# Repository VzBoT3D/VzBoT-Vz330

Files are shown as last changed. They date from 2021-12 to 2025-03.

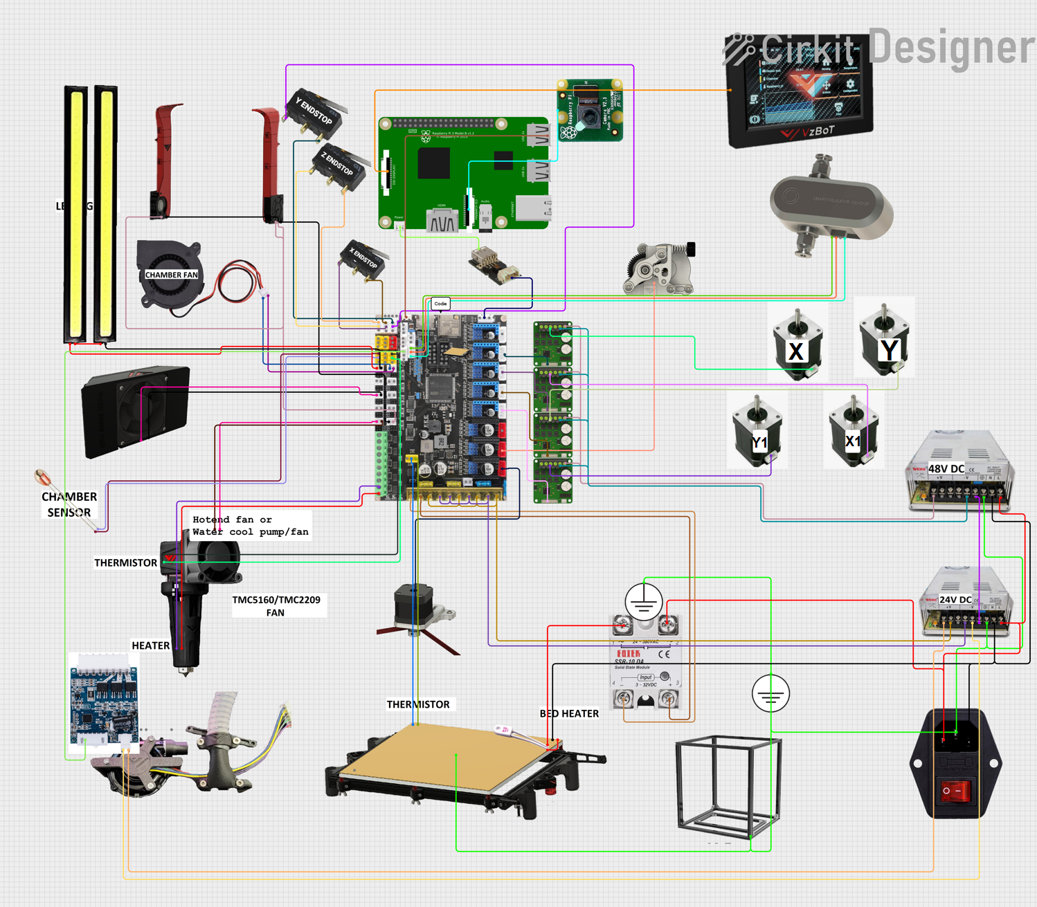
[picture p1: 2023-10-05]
Wiring Diagram/VZBOT 330 WIRING DIAGRAM AWD WITH CPAP.png

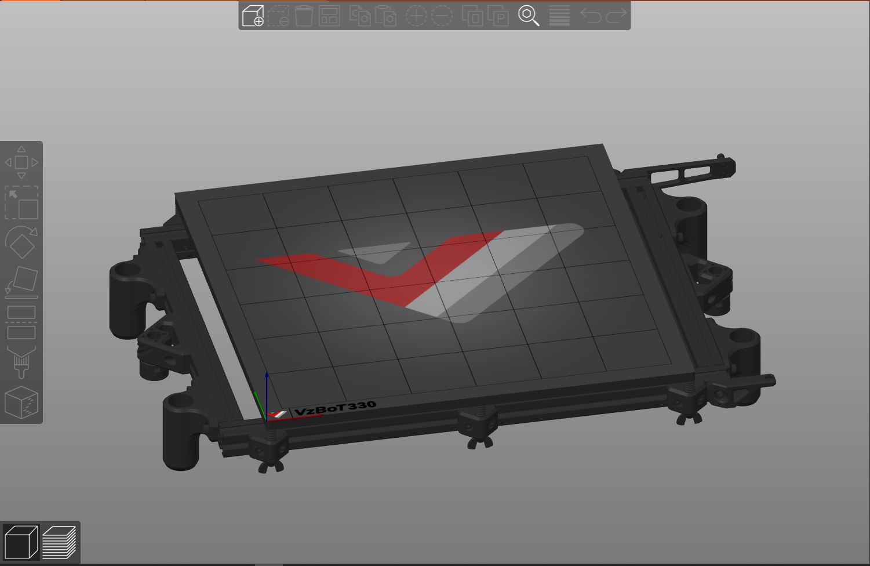
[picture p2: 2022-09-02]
Slicer/Theme/PrusaSlicer-SuperSlicer/Gallery/Vz330_bed_showcase.JPG

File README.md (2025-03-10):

# VzBoT <a href='https://ko-fi.com/vez3d' target='_blank'>Buy Me a Coffee at ko-fi.com</a> 

Discord Invite (https://discord.gg/KWZWvCMxCq)

High speed, moderately sized 3D-printer, based on the TronXY XS5(A) CoreXY frame,
but can be easily adapted for other 2020 aluminium extrusion frames.

You can find the complete web model without CAD-Software here: 
- [Printed Vz-330](https://a360.co/3FtdnGd)  
- [Full CNC AWD Vz-330](https://a360.co/4iu8HhW)

Vz-330-printed

Buy the full printer kit here: <https://s.click.aliexpress.com/e/_DkFwymp>

# Looking For Guides?

The VzBoT team has been working on our own docs for helping with your assembly of the machine. For the most upto date guides they can be found on the [VzBoT Docs][].

[VzBoT Docs]: https://docs.vzbot.org/

# What is the VzBoT?
The VzBoT is a high speed, moderately sized 3d Printer. Originally based on the TronXY X5S / X5SA Frame, this printer was aimed at those who wanted more performance out of their 330x330mm sized CoreXY 3D-printer.

Since this era, the VzBoT project has come very far. With CNC aluminum parts and a full kit with custom high performance hotend, the project has evolved at a lightning pace to be one of the fastest printers out there.

The printers
Originally, the VZ project started with a Vz-330 by Simon Vez. Recently, Guillaume has developed his iteration of the VzBoT. This printer aims to address a few compromises with the larger sized printer, by using a 235x235 bed size (ender 3 sized). This makes sourcing the parts for this printer relatively easy. Combined with the AWD functionality (all wheel drive, 2 motors on X and 2 on Y) and shorter belt loops, this printer is for those who thrive to be the fastest.

# What will a VzBoT set me back in terms of money?
Originally, as of start of 2022, a Vz-330 would set you back as follows:

800$ if you source really well and efficiently (budget)
1000$ for the average VzBoT
1500$ for the whole shablam with alu parts, 48v, all extras etc.

Add 100-150$ for panels, and you've got yourself a very nice 3d printer.

Unfortunately, due to inflation, and other costs, this price may be a higher (think 100-200$).

Additionally, a Vz-235 will be less expensive, due to the smaller size and easily source able parts.

# Where can you buy and find parts?
 We have 2 official manufacturers for parts. Mellow 3D and F3D racing in Germany. There are resellers and we will try to keep this list up to date. Please visit the reseller section

 - F3D Racing: https://f3d-racing-fdm.myshopify.com/
 - Aliexpress and Taobao:  [Mellow Store](https://www.aliexpress.com/store/1531088)

# What is AWD (All wheel drive)?
In conventional CoreXY machines, a 2WD setup is used. This setup utilizes 2 stepper motors at the back or front of the machine. Recently, the VzBoT project has adapted the AWD setup! This setup utilizes 2 motors on X, and 2 on Y, doubling the amount of motors for the XY plane. What are the advantages of this setup? Let's go over them:

- Having two motors on one belt allows for a shorter effective belt length. This leads to less belt stretch, which usually gives better input shaper results.
- The maximum useable acceleration is about 1.5x higher compared to 2WD due to the added torque.

We recommend using the LDO-42STH48-2504AC or 2504AH 1.8deg motors, as they give the best performance for the VzBoT's usecase.

This project is licensed as


https://creativecommons.org/licenses/by-nc/4.0/

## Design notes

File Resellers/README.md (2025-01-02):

List of resellers (this will be updated as we will deploy elwhere)

## Europe:

- Danemark: [3DO.dk](https://3do.dk/) 
- Germany: [CR-3D.de](https://www.cr3d.de/)
- Germany: [Meltbro](https://meltbro.de/mellow-vzbot-awd-330-3d-drucker-bausatz-metall-komponenten-golitath-hotend-hextrudort.html)
- Poland: [X3Dshop](https://x3dshop.com/products/drukarka-3d-mellow-vzbot-330-kit-1)

## Australia:
- [raven3dtech.com.au](https://raven3dtech.com.au/product/mellow-goliath-air-water/)

## Canada 
- [Northprint3d.ca](https://northprint3d.ca/product/vzbot-mellow-goliath-lsd-hotend/) |Only For Goliath|

## USA:
- [Provok3D](https://provok3d.com/vzbot-2/?v=0a10a0b3e53b)
- [3Dprintedprinter](https://3Dprintedprinters.com) 
- [Genericprinter](https://www.genericprinter.com/product/goliath-air-water-v2-hotend/)
- [Print3Dshop.org](https://print3dshop.org/)
- [Fabreeko](https://www.fabreeko.com/collections/hot-ends/products/vz-bot-goliath-hot-end-by-mellow)

## More to come..

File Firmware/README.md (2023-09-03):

- It is meant to work with Mellow Fly Super8 board with TMC5160 HV on XY and TMC2209 on E and Z

# Note for Super 8 Pro with STM32h723 Chip:
## If you are having random MCU disconnection/shutdown, please switch to software SPI, by commenting out the "spi_bus: spi1a" line on each 5160s section and uncomment those 3 lines:

- spi_software_mosi_pin: PB5 
- spi_software_miso_pin: PB4 
- spi_software_sclk_pin: PB3 

# Useful links:
- Super8 and Super8 Pro Documation: https://teamgloomy.github.io/fly_super8_general.html
- Super8 Std Klipper info: https://mellow.klipper.cn/#/board/fly_super8/
- Super8 Pro Klipper info: https://mellow.klipper.cn/#/board/fly_super8_pro/

# DISCLAIMER
- The macro files are REQUIRED for our printer.cfg to work with klipper.
- Its also REQUIRED to add a "Linux Process" to klipper, See the "Install the rc script" and "Building the micro-controller code" section [https://www.klipper3d.org/RPi_microcontroller.html]

# Macros information: DO NOT USE THE SPEED MACROS WITHOUT READING THIS.
## Speed Macros Explanation
Explanation: 
- 1st line: Steps << number of times it will do the stop and go, 100 times in the below case>>
- 2nd line: Velocity/Speed << The speed/velocity at which you want to test. 1000mms here>>
- 3rd line: safety distance << the safety distance in mm that the print head will not go from X max and Y max defined on your printer config>>	
- 4th line: Starting Accel << the starting acceleration value for the test. 10K here>>	

### Credits to DoubleT on Discord for his help on these macros

 [gcode_macro ACCELL_TEST_X]
 
gcode:

    {% set steps = params.STEPS|default(100)|int %}
    {% set speed = params.VELOCITY|default(1000)|float * 60 %}
    
    {% set inset = 10.0|float %} 
    {% set accel = 10000|int %} 
    {% set maxX = printer.configfile.settings.stepper_x.position_max|float - inset %}
    {% set maxY = printer.configfile.settings.stepper_y.position_max|float - inset %}
    {% set minX = printer.configfile.settings.stepper_x.position_min|float + inset %}
    {% set minY = printer.configfile.settings.stepper_y.position_min|float + inset %}

    SAVE_GCODE_STATE NAME=accelltest_state

    SET_VELOCITY_LIMIT ACCEL={accel} 
    SET_VELOCITY_LIMIT ACCEL_TO_DECEL={accel}
    G28
	G1 Z5
    G1 X{minX} Y{minY} F{speed} 

    {% for INTERVAL in range(steps) %}
        {% set eff = accel + (INTERVAL * 1000) %} 
        SET_VELOCITY_LIMIT ACCEL={eff} 
        SET_VELOCITY_LIMIT ACCEL_TO_DECEL={eff}
        G1 X{minX} Y{minY} F{speed}  
        G1 X{maxX} Y{maxY} F{speed}  

    {% endfor %}    

    RESTORE_GCODE_STATE NAME=accelltest_state 

[gcode_macro ACCELL_TEST_Y]

gcode:

    {% set steps = params.STEPS|default(100)|int %}
    {% set speed = params.VELOCITY|default(1000)|float * 60 %}

    {% set inset = 10.0|float %}
    {% set accel = 10000|int %}
    {% set maxX = printer.configfile.settings.stepper_x.position_max|float - inset %}
    {% set maxY = printer.configfile.settings.stepper_y.position_max|float - inset %}
    {% set minX = printer.configfile.settings.stepper_x.position_min|float + inset %}
    {% set minY = printer.configfile.settings.stepper_y.position_min|float + inset %}

    SAVE_GCODE_STATE NAME=accelltest_state

    SET_VELOCITY_LIMIT ACCEL={accel} 
    SET_VELOCITY_LIMIT ACCEL_TO_DECEL={accel}
    G28
	G1 Z5
    G1 X{minX} Y{minY} F{speed} 

    {% for INTERVAL in range(steps) %}
        {% set eff = accel + (INTERVAL * 1000) %} 
        SET_VELOCITY_LIMIT ACCEL={eff} 
        SET_VELOCITY_LIMIT ACCEL_TO_DECEL={eff}
        G1 X{maxX} Y{minY} F{speed}  
        G1 X{minX} Y{maxY} F{speed}  

    {% endfor %}    

    RESTORE_GCODE_STATE NAME=accelltest_state

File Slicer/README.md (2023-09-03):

The Vzbot team has moved Slicers, currently with OrcaSlicer you can download printer ready Profiles!
https://github.com/SoftFever/OrcaSlicer/releases

Thanks to SoftFever for the wondeful Slicer!

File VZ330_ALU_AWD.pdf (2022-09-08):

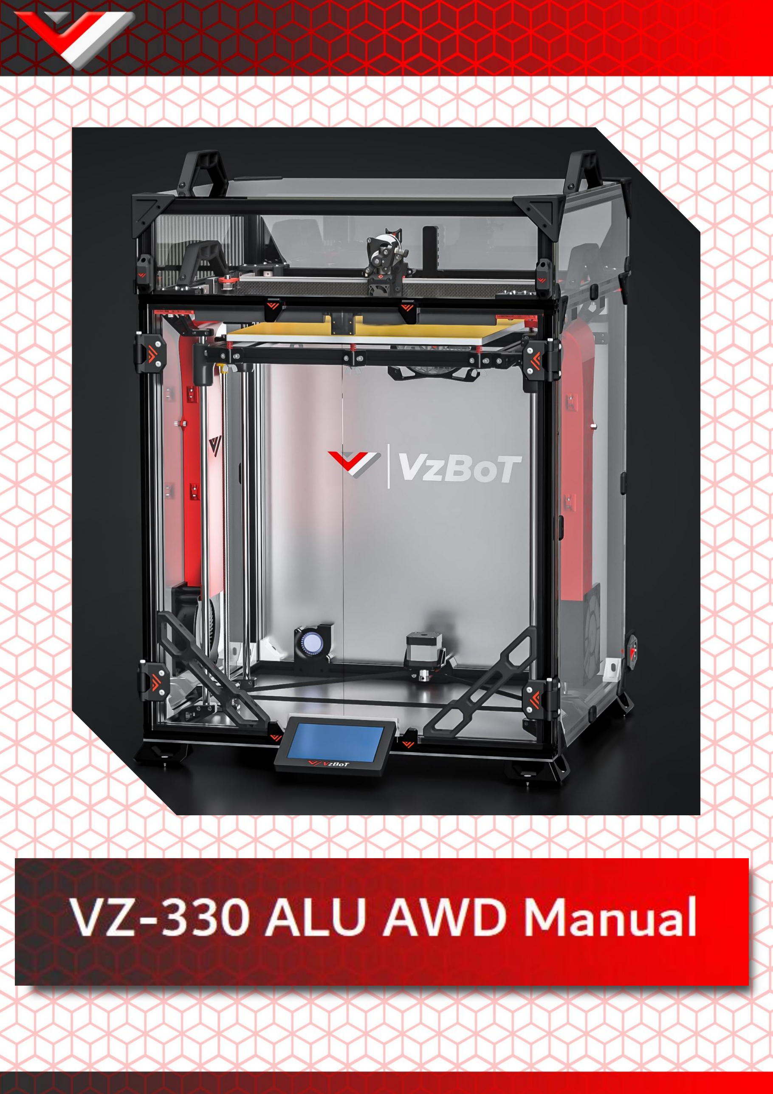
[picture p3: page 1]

## About

This manual is intended for the aluminum parts for VZ330 as sold by F3D-Racing and Mellow. The aluminum parts are interchangeable with the printed parts, some additional hardware is required when purchasing the motor mounts and idler mounts. Furthermore some printed parts are required in order to mount your new sexy parts!

Beware, VZ330 was never designed around AWD like VZ235. Because of this the design team was left with the frame as constraint. Due to which it was not possible to have a design that did not limit y travel for the VZ330 printhead. There is a 10mm loss in Y travel coming from 330mm.

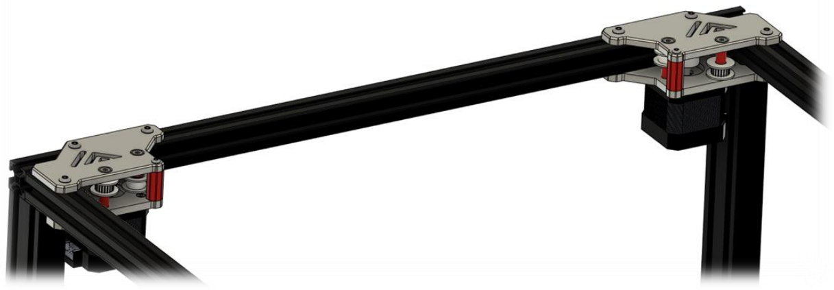
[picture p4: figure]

https://f3d-racing-fdm.myshopify.com/collections/vzbot-vz330

https://mellow.nl.aliexpress.com/store/1531088?spm=a2g0o.detail.1000007.1.67f7726dJR pvIK\ (https://mellow.nl.aliexpress.com/store/1531088?spm=a2g0o.detail.1000007.1.67f7726dJRpvIK/)

*Disclaimer: VzBoT is an opensource passion project, this manual is not definitive, and we try to make it as polished as possible. Fortunately, we all make errors so use common sense when following this guide.

## Print settings:

We recommend printing all parts in ABS, ASA or similar material to be able to withstand the high heat environment in the printer enclosure.

Print settings should always be tuned for your own material and tested for decent strength and layer adhesion.

We recommend the following settings:

For non-moving parts:

Layer height: 0.2mm

Layer with: 0.4 to 0.6 mm

Number of walls: 4

Infill percentage: 40 to 50 %

Top/bottom layers: 5

For moving parts:

Layer height: 0.2mm

Layer with: 0.4 to 0.6 mm

Number of walls: 4

Infill percentage: 30 to 40 % depending on your material

Top/bottom layers: 5

## AWD Motormounts/Idlers

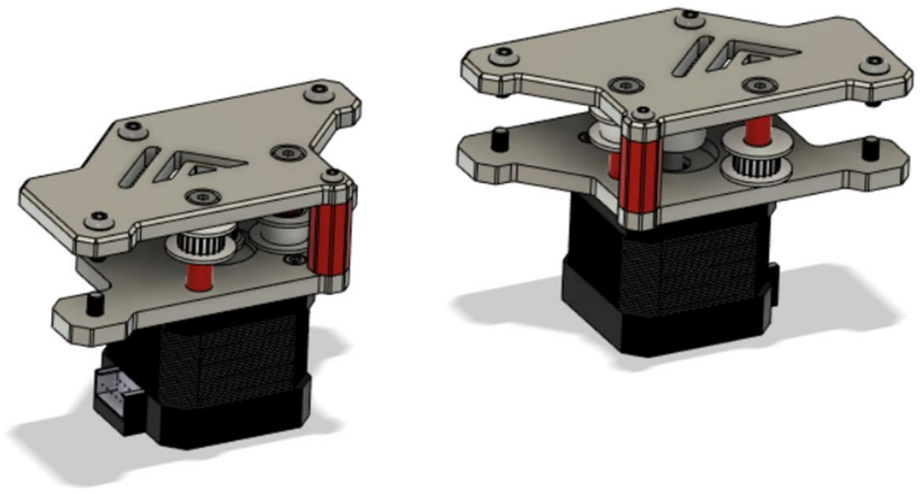
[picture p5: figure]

Bom:

Material | Quantity | Notes
M3 30mm | 2
M3 6mm | 6
M4 10mm | 10 | +2 for mellow version
M4 T-nut | 10
Shoulder bolt 5mmx20mm [M3] | 4 | M3 threading with 6mm of threaded length, if longer grind down the ends. Correct shoulder bolts available at mellow & F3D
GT2 Toothed idler | 2
Gt2 Smooth idler | 2
GT2 motor pulley | 2

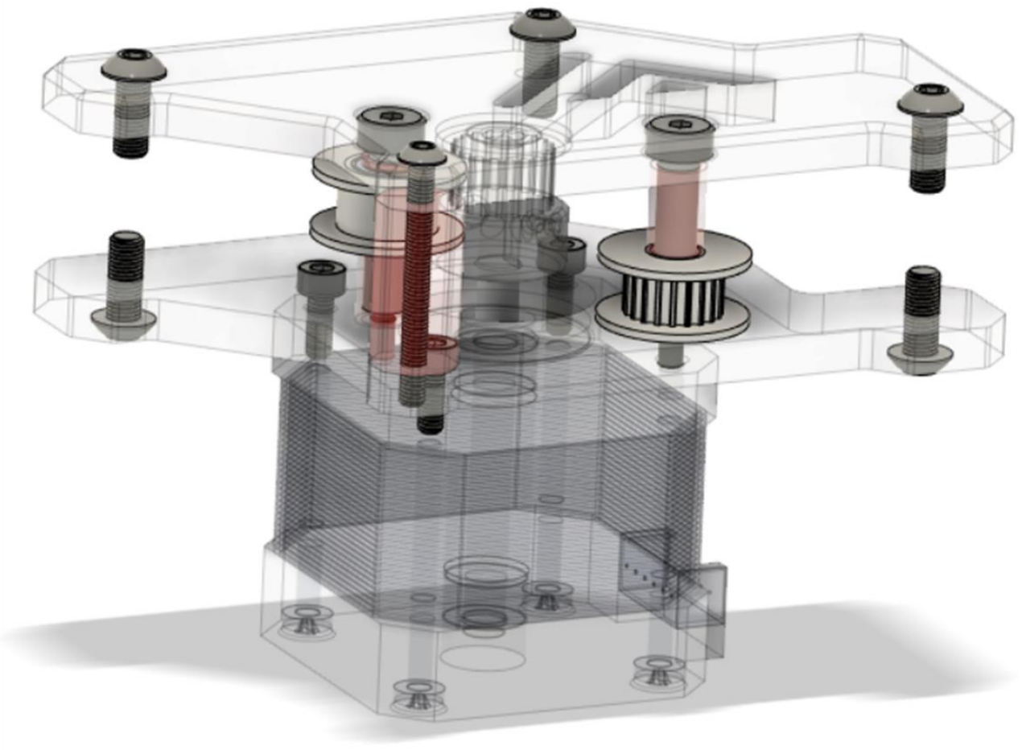
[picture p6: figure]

STL files:

File name | Amount to print
Spacer long | 4
Spacer short bottom | 2
Spacer short top | 2
Spacer M3 corner | 2

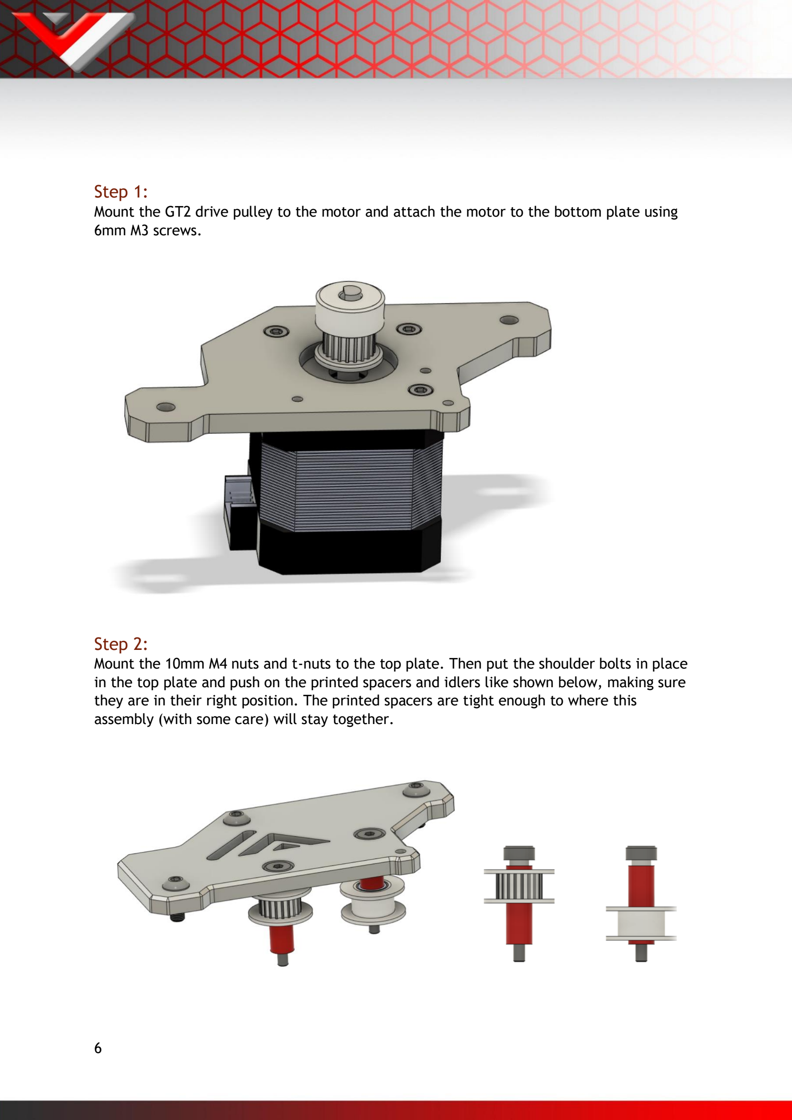
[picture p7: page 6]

Step 1:
Mount the GT2 drive pulley to the motor and attach the motor to the bottom plate using 6mm M3 screws.
Step 2:
Mount the 10mm M4 nuts and t-nuts to the top plate. Then put the shoulder bolts in place in the top plate and push on the printed spacers and idlers like shown below, making sure they are in their right position. The printed spacers are tight enough to where this assembly (with some care) will stay together.

Step 3:
Attach the bottom assembly to the printer frame using 10mm M4 screws and t-nuts. After this attach the top assembly from the previous step loosely. Make sure the shoulder bolts thread before tightening all screws.

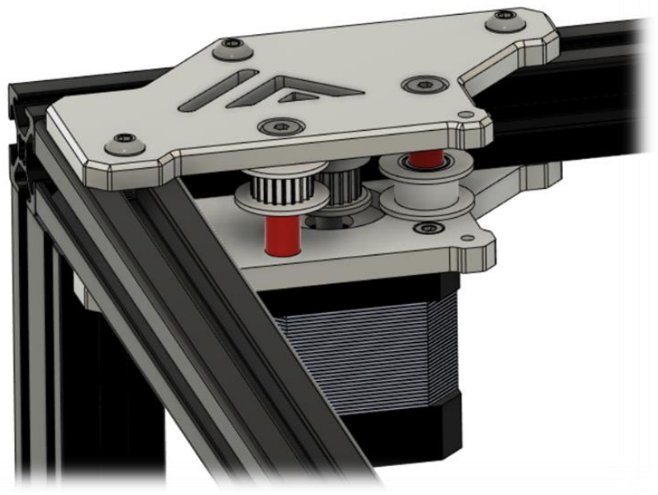
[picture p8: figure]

Step 4:
Insert the printed corner spacer and install the 30mm M3 like shown below.

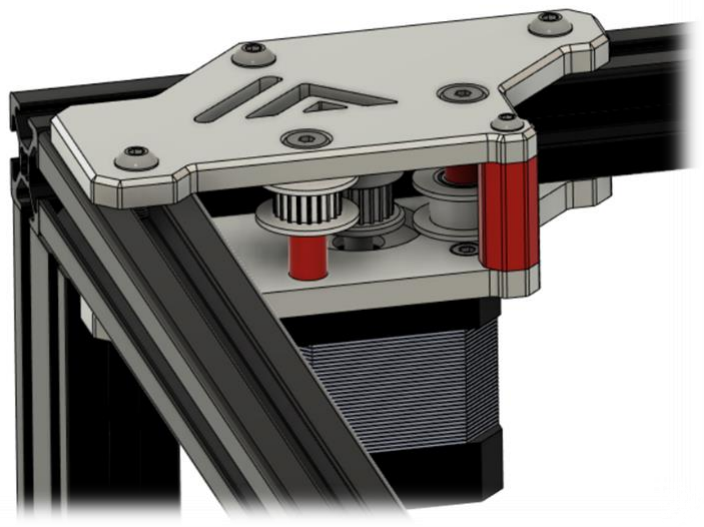
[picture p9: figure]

Step 5:
Repeat the same process for the other side making sure to put the idlers in their correct position.

## Firmware:

Klipper, RRF and Marlin natively support AWD for Corexy kinematics. For a Klipper example Cfg suited for AWD check the VZ235 Github page.

https://github.com/VzBoT3D/VzBoT-Vz235/tree/main/Firmware

XY motion Example CFG Klipper:
[stepper_y]

step_pin: PE11

dir_pin: !PE10

enable_pin: !PE9

rotation_distance: 40

microsteps: 16

full_steps_per_rotation: 200

endstop_pin: ^PB13

position_endstop: 0

position_max: 235

homing_speed: 25

homing_retract_dist: 0

[tmc5160 stepper_y]

spi_bus: spi4

cs_pin: PE7

interpolate: false

#diag1_pin: PB14

run_current: 1.6

[stepper_y1]

dir_pin: !PC13

enable_pin: !PE5

step_pin: PE6

rotation_distance: 40

microsteps: 16

full_steps_per_rotation: 200

[tmc5160 stepper_y1]

spi_bus: spi4

cs_pin: PC14

interpolate: false

#diag1_pin: PB14

run_current: 1.6

[stepper_x]

step_pin: PD8

dir_pin: !PB12

enable_pin: !PD9

rotation_distance: 40

microsteps: 16

full_steps_per_rotation: 200

endstop_pin: ^PB14

position_endstop: 0

position_max: 235

homing_speed: 25

homing_retract_dist: 0

[tmc5160 stepper_x]

spi_bus: spi4

cs_pin: PE15

#diag1_pin: PB13

interpolate: false

run_current: 1.6

[stepper_x1]

dir_pin: !PE4

enable_pin: !PE3

step_pin: PE2

rotation_distance: 40

microsteps: 16

full_steps_per_rotation: 200

[tmc5160 stepper_x1]

spi_bus: spi4

cs_pin: PC15

interpolate: false

#diag1_pin: PB14

run_current: 1.6

## Setup and tuning:

After finishing the build one must take care to properly set up the AWD system. It is important to “sync the motors”. In order to achieve this it is advised to use the following macro’s in klipper:

[gcode_macro enable_stepper]

gcode:

SET_STEPPER_ENABLE STEPPER=stepper_x ENABLE=1

SET_STEPPER_ENABLE STEPPER=stepper_x1 ENABLE=1

SET_STEPPER_ENABLE STEPPER=stepper_y ENABLE=1

SET_STEPPER_ENABLE STEPPER=stepper_y1 ENABLE=1

[gcode_macro disable-steppers]

gcode:

m84

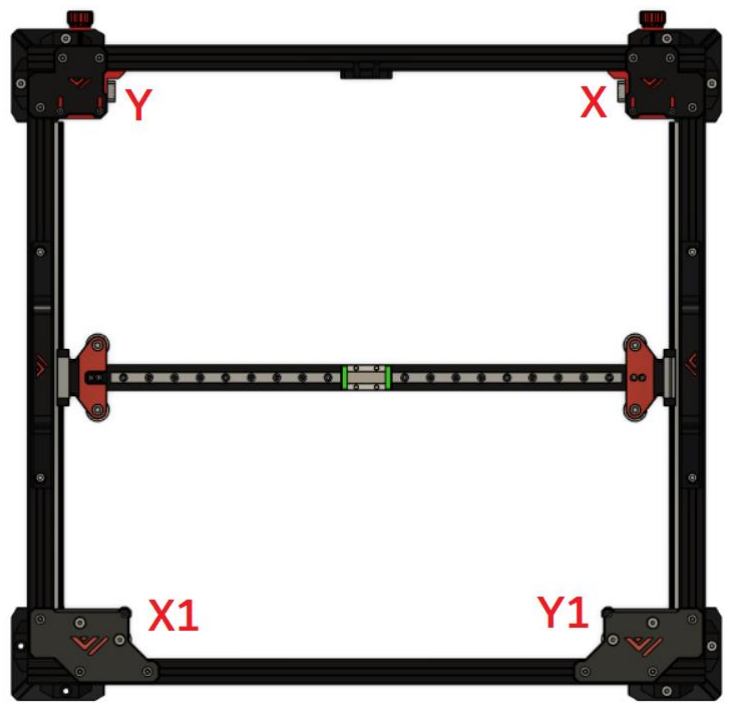
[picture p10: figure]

Step 1:
Set belt tension like on a normal 2WD VZ330.
Step 2:
Loosen the grubscrews on one of each set of motors, make sure the grub screws will not be on the flat side of the stepper shaft.
Step 3:
Boot up the printer and order “enable stepper”.
Step 4:
Tighten the stepper grub screws and disable steppers again.

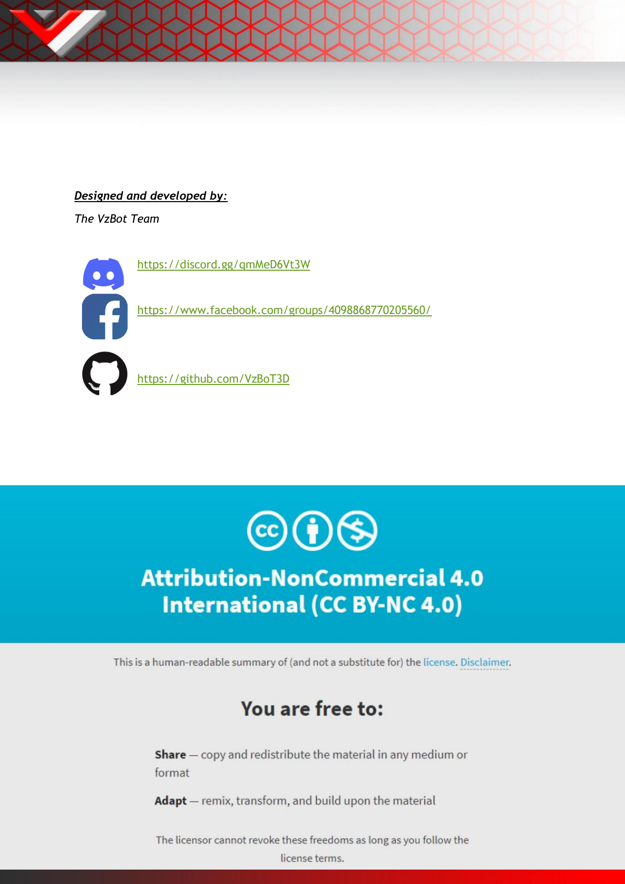
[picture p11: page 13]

Designed and developed by:

The VzBot Team

https://discord.gg/qmMeD6Vt3W

https://www.facebook.com/groups/4098868770205560/

https://github.com/VzBoT3D

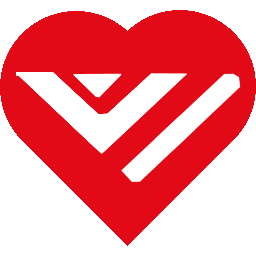
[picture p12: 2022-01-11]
Gallery/VzLoveAlt.png

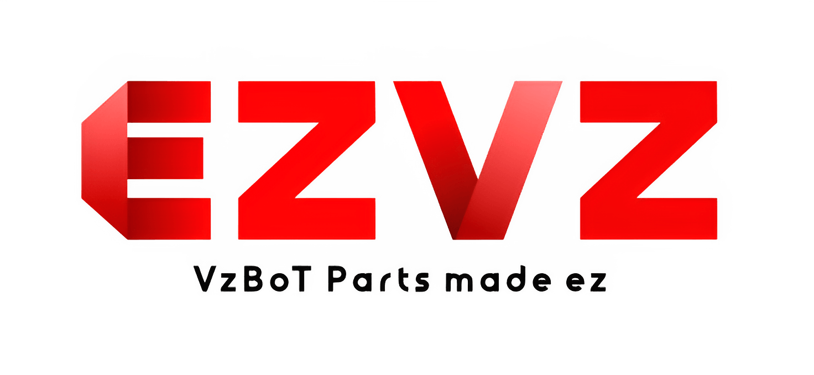
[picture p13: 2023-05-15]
Gallery/vDrdEWwl_2x.jpg

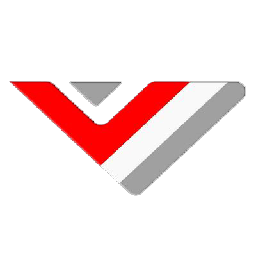
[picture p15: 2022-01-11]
Gallery/VzBoT.png

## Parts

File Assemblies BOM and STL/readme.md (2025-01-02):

# Assembly BOM's and STL's

This folder contains the BOM and STL files for each individual assembly specified in the [CAD](/CAD) folder.

You can explore the folders for the assemblies you are interested in, or [download this folder](https://download-directory.github.io/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) in full.

## Printing

Settings for printing can be found on the [Print settings](https://docs.vzbot.org/general/misc-info/print-settings/) VzBoT Docs page.

The quantity of each printed part may differ. A selection of parts are available in different variants to suit the needs of more than one possible BOM or hardware setup. These are mostly supplied for retro-compatibility, and no longer recommended for new builds. New builds are encouraged to follow the standard BOM, like the Mellow3D kits. 

Please carefully read through the filenames to assess whether the file or part applies to your machine or not.

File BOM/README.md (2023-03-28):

# Work in progress, please tell us any errors
https://docs.google.com/spreadsheets/d/1eNbgQ2HAe7iDxFRou1gHZOtjP1PLiPEpZYigivr-bK0/edit?usp=sharing

Frame size selector

https://docs.google.com/spreadsheets/d/1eNbgQ2HAe7iDxFRou1gHZOtjP1PLiPEpZYigivr-bK0/edit#gid=0

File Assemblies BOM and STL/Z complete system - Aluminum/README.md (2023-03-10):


For instructions, BOM and STL list: see the pdf manual 

Both VZ330 and VZ235 share the same Z-system, though not all parts are the same for both. The manual covers both as functional the only difference between the two is the chain mount. Do mind when ordering the kit that you order the right one specific to your machine!

If you want to re-use your old LM10LUU bearings and not buy LMK10LUU, you can print this adapter found in the STL folder


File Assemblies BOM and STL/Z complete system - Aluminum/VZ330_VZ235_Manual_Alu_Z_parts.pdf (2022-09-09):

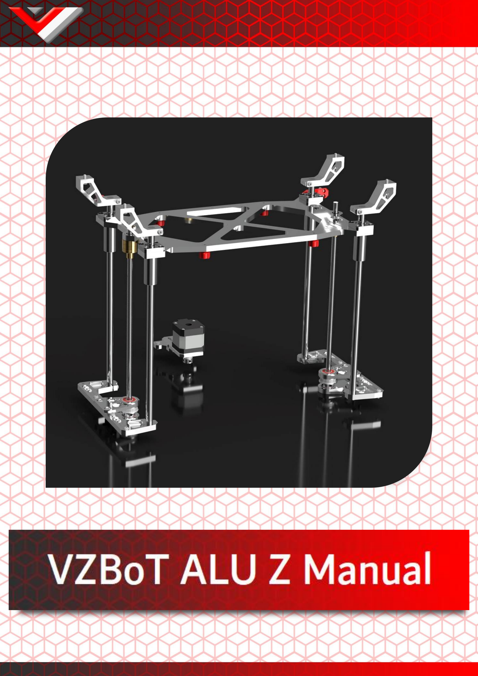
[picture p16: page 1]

## About

This manual is intended for the aluminum parts for VZ330 and VZ235 as sold by F3D-Racing and Mellow. This manual will cover both VZ235 and VZ330 as the parts are mounted the same, mind that they are different in dimension. The aluminum parts are interchangeable with the printed parts, some additional hardware is required. Furthermore some printed parts are required in order to mount your new sexy parts!

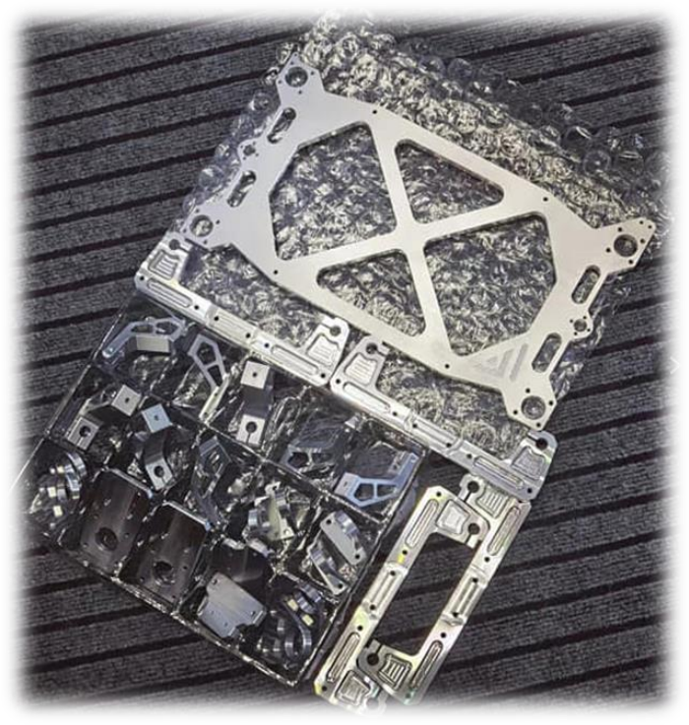
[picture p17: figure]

https://f3d-racing-fdm.myshopify.com/collections/vzbot-vz330

https://mellow.aliexpress.com/store/group/VzBoT/1531088_40000000168256.html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 (https://mellow.aliexpress.com/store/group/VzBoT/1531088_40000000168256.html)

*Disclaimer: VzBoT is an opensource passion project, this manual is not definitive, and we try to make it as polished as possible. Fortunately, we all make errors so use common sense when following this guide.

## Print settings:

We recommend printing all parts in ABS, ASA or similar material to be able to withstand the high heat environment in the printer enclosure.

Print settings should always be tuned for your own material and tested for decent strength and layer adhesion.

We recommend the following settings:

For non-moving parts:

Layer height: 0.2mm

Layer with: 0.4 to 0.6 mm

Number of walls: 4

Infill percentage: 40 to 50 %

Top/bottom layers: 5

For moving parts:

Layer height: 0.2mm

Layer with: 0.4 to 0.6 mm

Number of walls: 4

Infill percentage: 30 to 40 % depending on your material

Top/bottom layers: 5

## Lower rod & leadscrew bracket

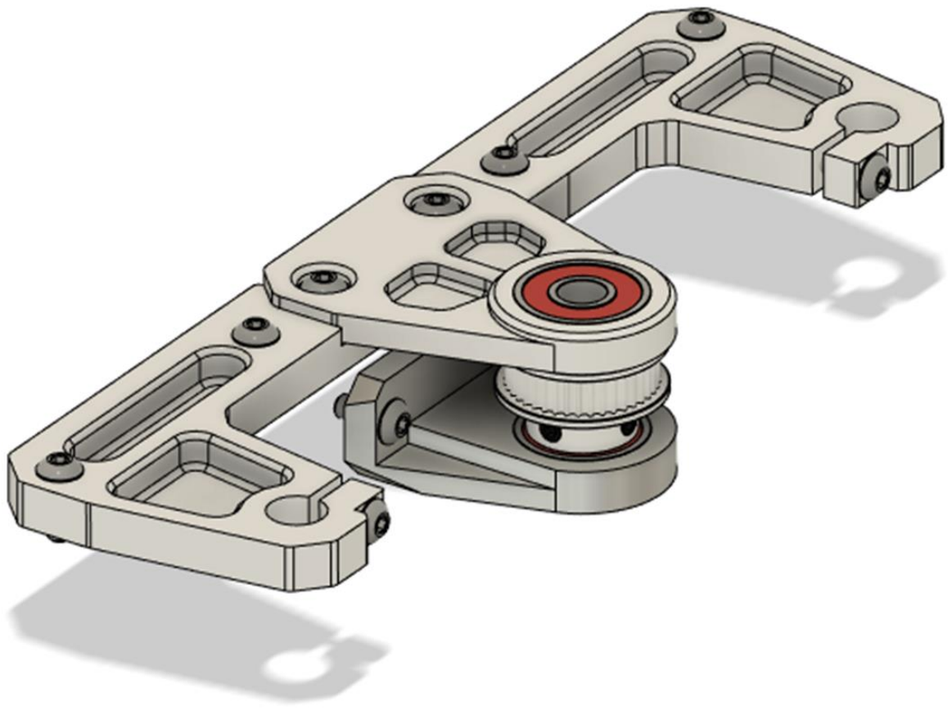
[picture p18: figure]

Bom:
Material | Quantity | Notes
10mm M4 | 4
12mm M4 | 16
608-2RS (skateboard) bearing | 4
GT2 40T 8mm bore Pulley | 2
10mm rods Vz-235: 300mm Vz-330: 500mm | 4
Belt GT2 closed, Vz-235: 860mm Vz-330: 1100mm | 1
Lead screw TR8 Vz-235 300mm Vz-330 500mm | 2

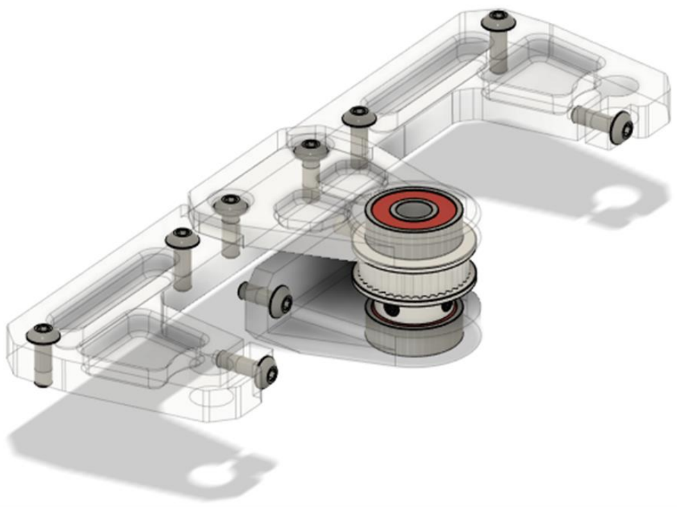
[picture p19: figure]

STL files:

File name | Amount to print
Z assembly alignment tool (either EVA/VZprinthead) | 1

Step 1:
Mount the top bracket with the 12mm M4 hardware to the frame loosely. Then mount the sliding rods with 12mm M4 screws and align the assembly to the frame using the printed “Z assembly alignment tool”. Be sure to secure all hardware. Be sure to either insert 2 T-nuts underneath the center two holes for the top leadscrew bracket or immediately mount the top bracket.

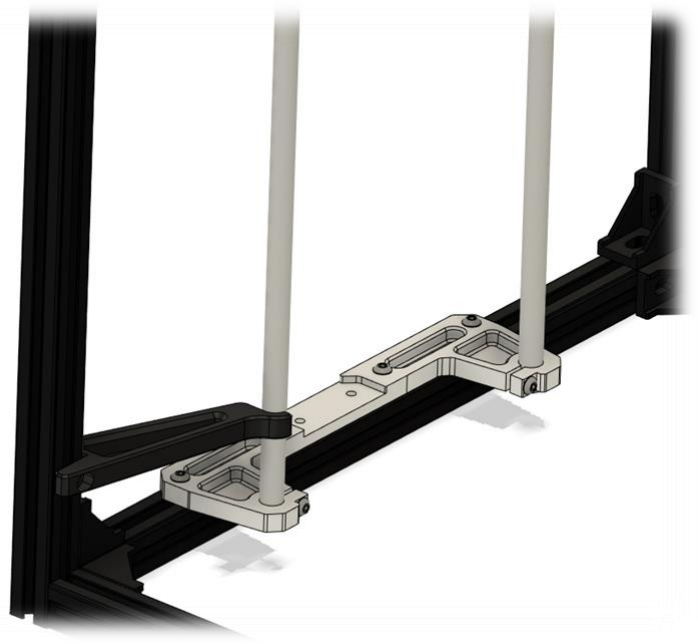
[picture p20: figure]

Step 2:
Mount the lower leadscrew bracket, using 2x 10mm M4 screws, loosely to the frame approximately in the correct position relative to the top bracket.

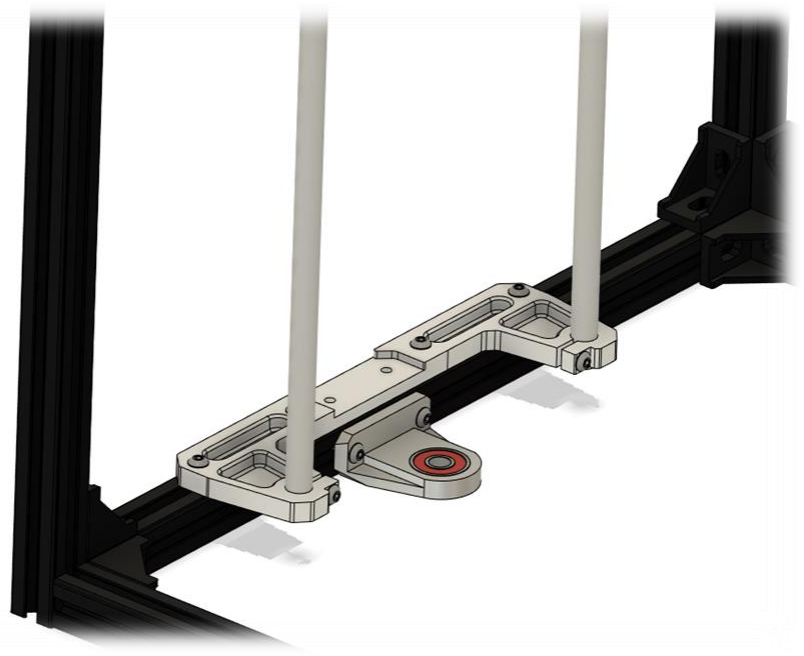
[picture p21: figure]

Step 3:
Mount the top leadscrew bracket to the assembly using 12mm M4 screws (skip when done in step one). Insert the pulley with the closed belt and insert the leadscrew. Then tighten the grub screws on the pulley. Lastly while making sure the leadscrew is perfectly straight up tighten the screws on the upper and lower leadscrew brackets. This can be checked by measuring the distance on both sides between the leadscrew (top position) and the 10mm Rods.

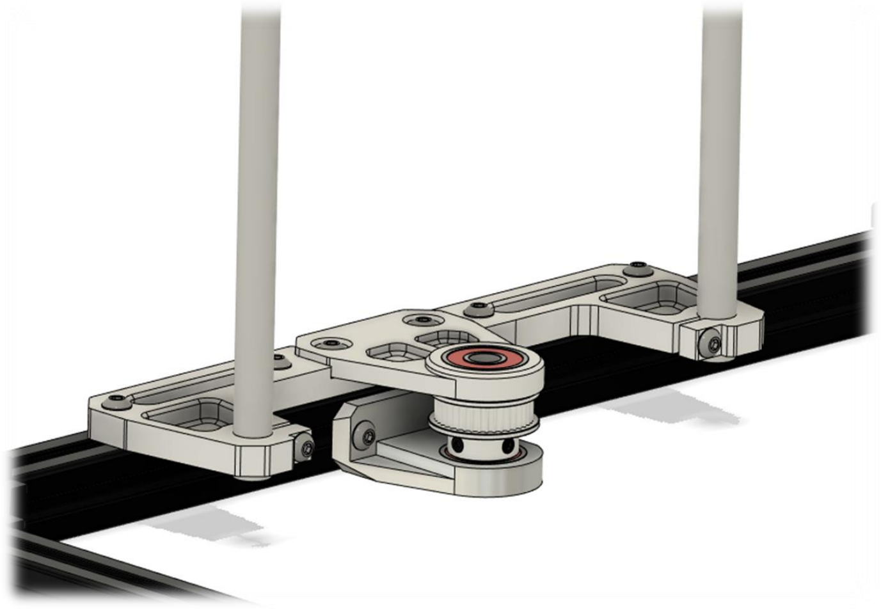
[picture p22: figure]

Step 4:
Repeat steps 1 through 3 for the other side.

## Bed assembly

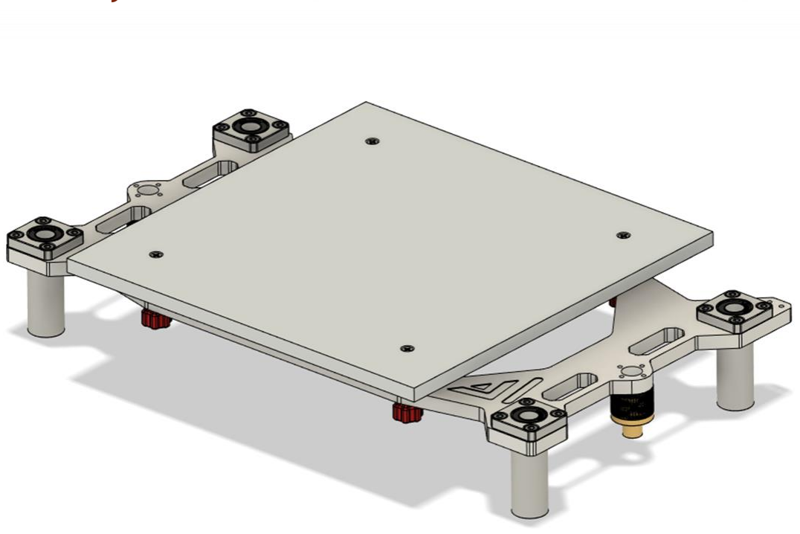
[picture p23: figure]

Bom:

Material | Quantity | Notes
M4 8mm | 16
M3 8mm | 16
M3 50mm | 4 | Countersunk for the bed
M3 nuts | 12
LMK10LUU | 4
Oldham coupler | 2 | Optional but highly advised
Leadscrew nut | 2

STL files:

File name | Amount to print
Bed level adjustment knobs | 4
Oldham couplers | optional


Step 1:
Mount the LMK10LUU using the M4 hardware to the bed frame. Then mount the Oldham couplers with the leadscrew nuts together with M3 hardware and mount that assembly to the bed frame using M3 hardware
Step 2:
Place the bed assembly in the rods and leadscrew.

Step 3:
Mount the bed plate to the bed frame using the 50mm countersunk M3 screws. When using a cast aluminum bed make sure it is well prepped before mounting. It is recommended to always be safe and inform yourself properly on how to apply a AC silicon heating pad.


## Top rod mounts


Bom:

Material | Quantity | Notes
M4 10mm | 4
M4 20mm | 4
M4 T-nut | 4


Step 1:
Mount the 10mm M4 screws and T-nuts to all top rod mounts and loosely turn in the 20mm M4 screws in the clamping mechanism.


Step 2:
Mount all top rod mounts to the rod first. Make sure the rod mount with the extra hole (for the Z limit switch) is in the back right of the printer like shown below. Finally tighten the rod holders to the frame with the pre-inserted M4 hardware.


Step 3:
After installing check the movement of the bed assembly by turning the leadscrews. This should operate smoothly. If not, place the bed assembly in the top most position, untighten all top rod holders and retighten to align the rods.

## Single z motor bracket


Bom:

Material | Quantity | Notes
M3 10mm | 4
M4 10mm | 4
M4 T-nut | 2
20t GT2 | 1
NEMA 17 stepper | 1

Step 1:
Mount the bracket shown below to the frame using the 10mm M4 screws and T-nuts. Make sure it is nicely centered in the middle of the frame.


Step 2:
Mount the stepper motor to the top bracket using the 10mm M3 screws. Attach the motor pulley like shown below.


Step 3:
Mount the previous assembly to the bracket on the frame using 10mm M4 screws.


Step 4:
With the motor in the furthest position, loop the belt around the motor pulley and tighten the belt. Be sure to check if the belt is horizontally parallel to the frame for smoothest operation.

## Z switch & bed chain

Vz-235:


Vz-330:


Bom:
Material | Quantity | Notes
M3 10mm | 4 (vz235) 2(vz330) | For Chain to chain mount (bot 235 and 330) and to bed support on Vz-235.
M3 6mm | 4 (Vz330) | (Vz-330 only) For chain mount to bed support
M3 8mm | 1 | For microswitch
M2 10mm | 2 | For microswitch
M3 40mm | 1
M3 nut | 3
Microswitch | 1


Vz-235: | Vz-330:

Both Vz-330 & Vz-235:

STL files:

File name | Amount to print
Printed z switch adapter | 1
Z-chain mount | 1

Step 1:
Mount the printed chain mount to the bed frame using 2x10mm M3 screws (Vz-2235) or 4x6mm M3 (Vz-330). Then mount the cable chain using 10mm M3 screws and nuts like shown below.


Step 2:
Mount the microswitch to the printed adapter using M2 screws. Then mount the assembly to the top rod holder using the 8mm M3. Finally screw in the 50mm M3 screw and nut like shown below. After setting the correct Z-height using the adjustment screw use the M3 nut to lock the screw in place in order to make sure the screw doesn’t drift off position.


Designed and developed by:

The VzBot Team

https://discord.gg/qmMeD6Vt3W

https://www.facebook.com/groups/4098868770205560/

https://github.com/VzBoT3D




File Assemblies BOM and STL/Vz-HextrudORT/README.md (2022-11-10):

Moved here: https://github.com/VzBoT3D/Vz-HextrudORT

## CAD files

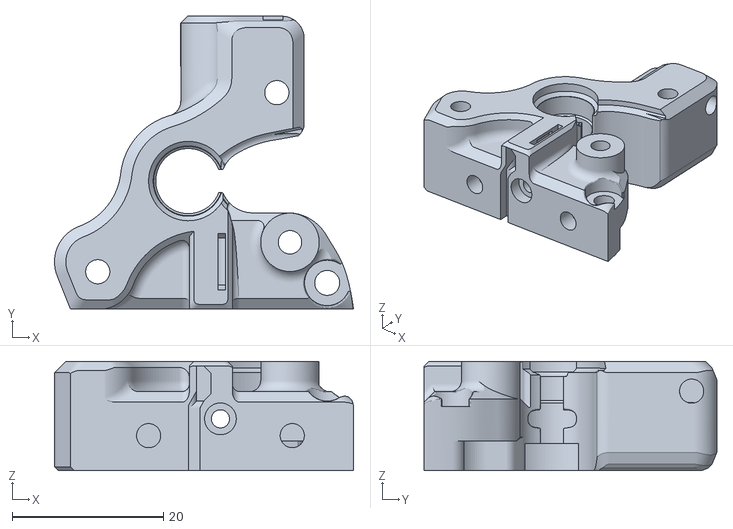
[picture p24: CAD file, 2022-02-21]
Assemblies BOM and STL/Vz-HextrudORT/STLs/ERCF version/main body-ERCF.stl
39.5 x 38.7 x 14.4

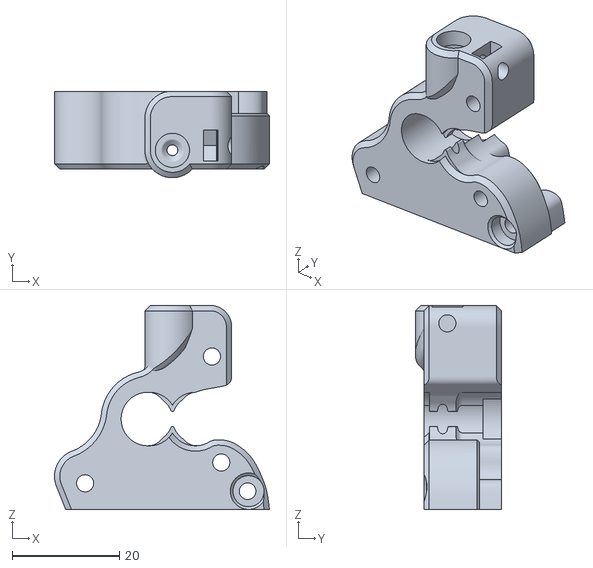
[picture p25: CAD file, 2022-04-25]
Assemblies BOM and STL/Vz-HextrudORT/STLs/main body low motor helical gears.stl
40.2 x 16.1 x 38.1

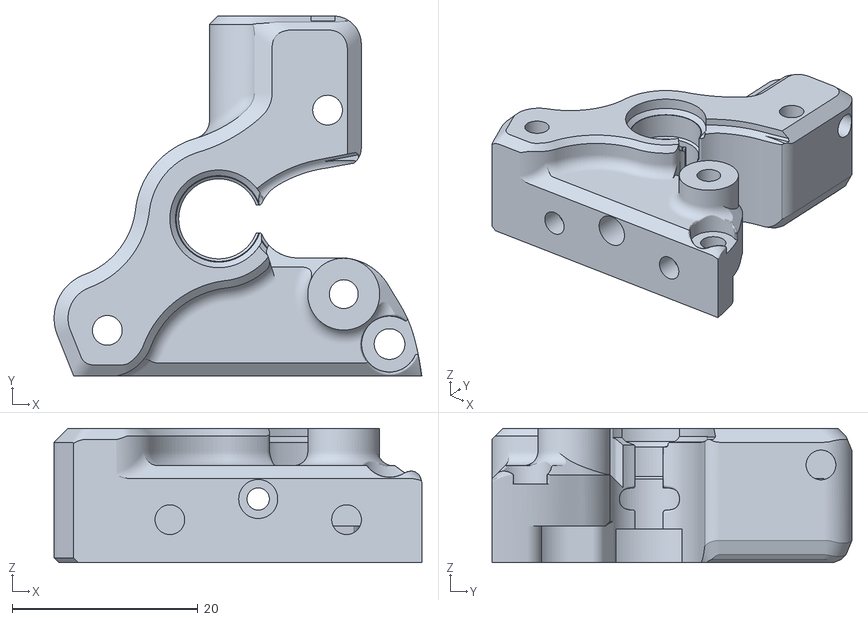
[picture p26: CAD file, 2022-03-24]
Assemblies BOM and STL/Vz-HextrudORT/STLs/main body.stl
39.5 x 38.7 x 14.4

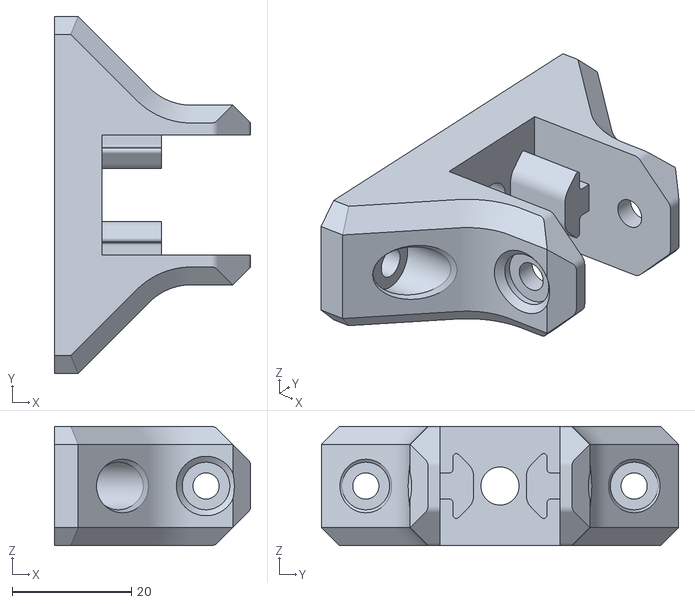
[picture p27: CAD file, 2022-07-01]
Assemblies BOM and STL/[Optional] Wall anchor/printer anchor frame side (1).stl
33.0 x 60.0 x 20.0

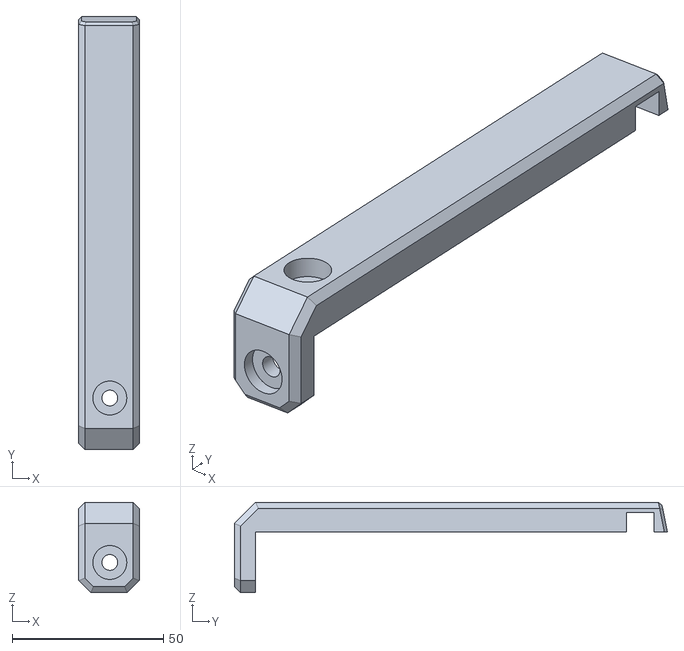
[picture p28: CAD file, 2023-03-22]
Assemblies BOM and STL/Alignment Tools/X Alignment Tool.stl
20.0 x 143.0 x 29.9

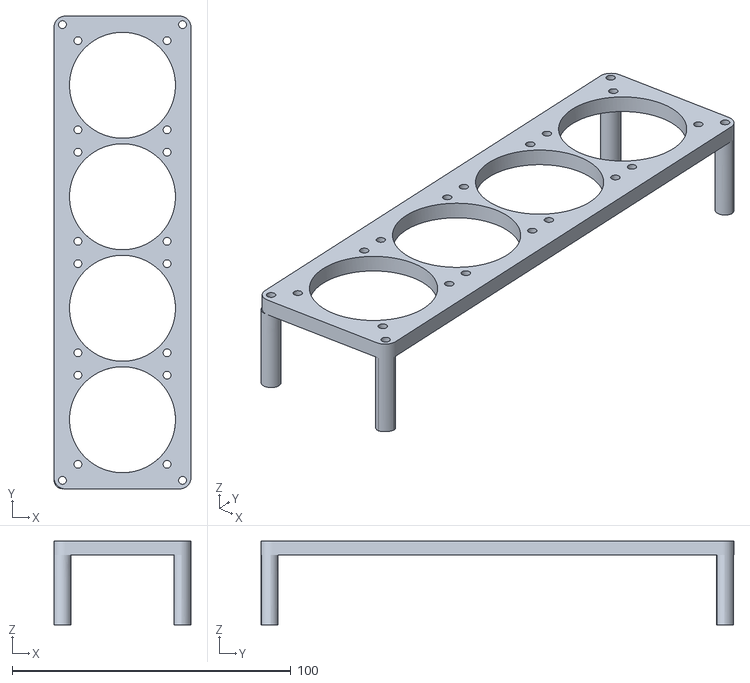
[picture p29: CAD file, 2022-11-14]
Assemblies BOM and STL/electronics/Back Electronic bay/Fly Super8/FlySuper8 fan cover.stl
49.1 x 169.6 x 30.0

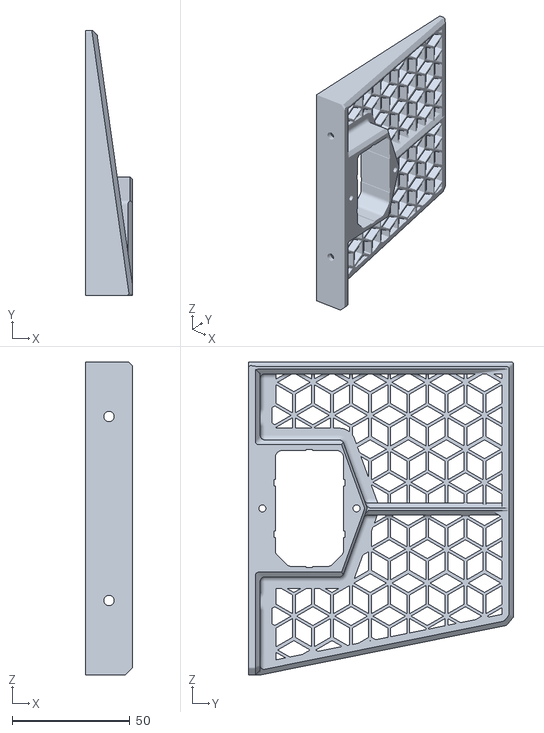
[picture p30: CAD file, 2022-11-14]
Assemblies BOM and STL/electronics/Back Electronic bay/Lower Grill right with powerswitch.stl
20.0 x 112.7 x 133.0

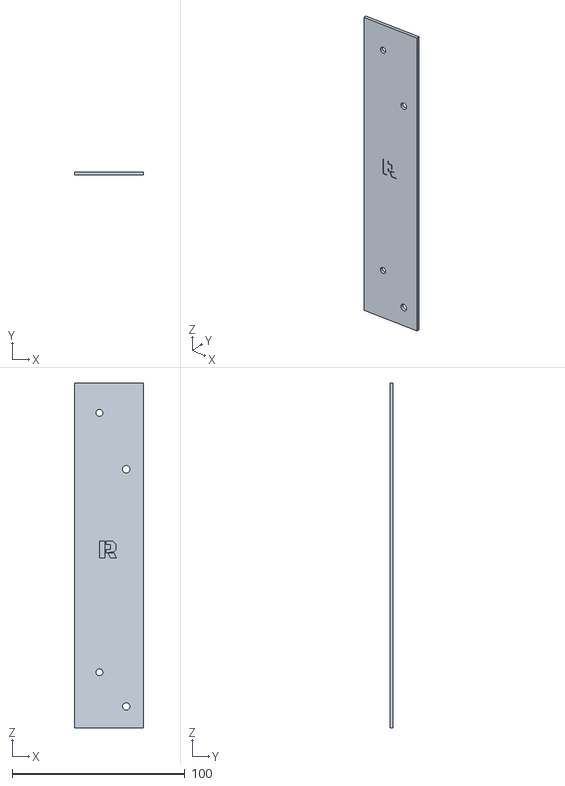
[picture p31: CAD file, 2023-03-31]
Assemblies BOM and STL/electronics/Back Electronic bay/PSU drilling template/PSU_drilling_template.stl
40.0 x 2.00 x 200.0

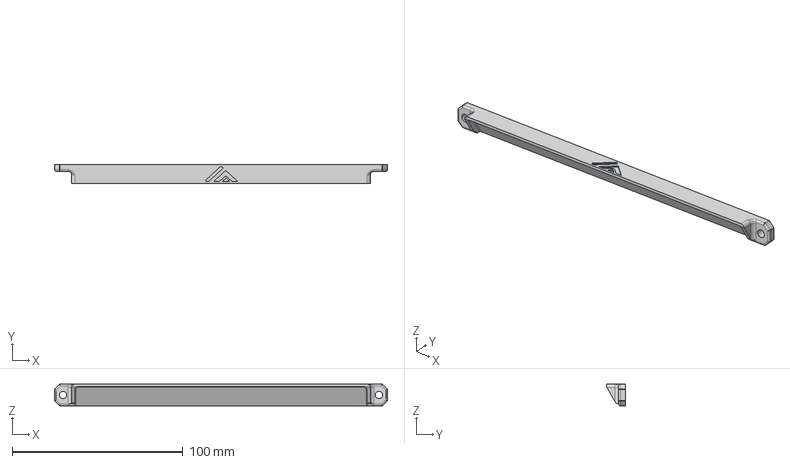
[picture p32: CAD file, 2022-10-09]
Assemblies BOM and STL/electronics/Front LED for AWD/Led mount.step
195.0 x 11.0 x 12.8 mm

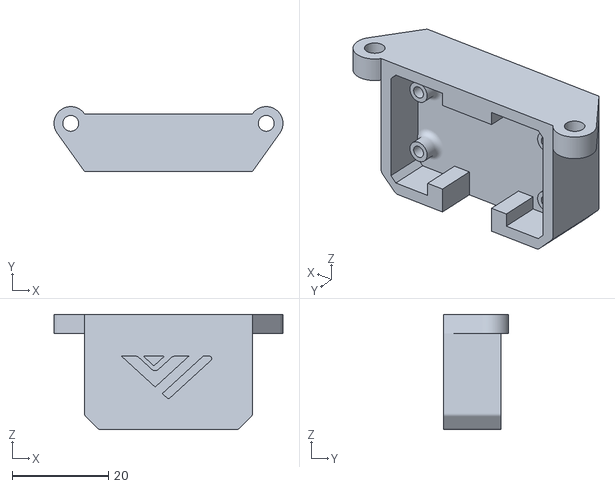
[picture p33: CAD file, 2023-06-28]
Assemblies BOM and STL/electronics/Mini 16mp USB camera mount/Mini cam mount-back.stl
47.7 x 13.5 x 24.0

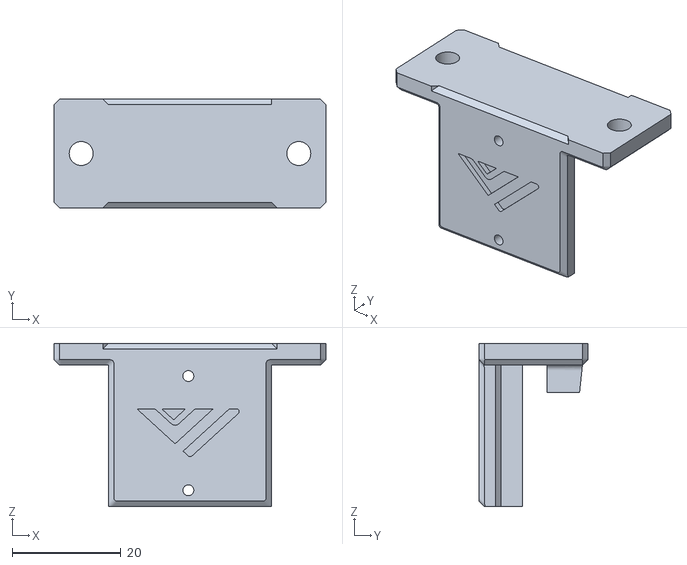
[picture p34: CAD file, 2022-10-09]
Assemblies BOM and STL/electronics/raspicam+CSItoHDMI high mount.stl
50.0 x 20.0 x 30.0

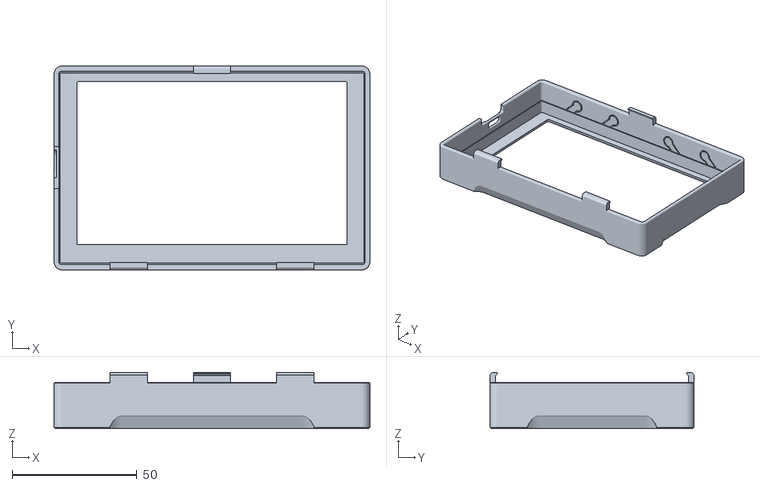
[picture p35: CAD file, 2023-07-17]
Assemblies BOM and STL/electronics/Screen Mount/Mellow-Fly Version/Front cover.stl
126.7 x 81.9 x 22.5

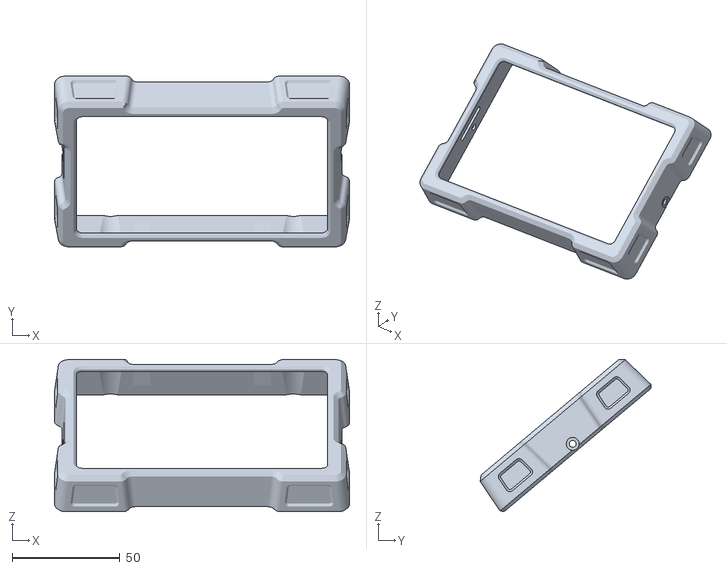
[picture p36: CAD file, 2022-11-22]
Assemblies BOM and STL/electronics/Screen Mount/screen cover.stl
136.9 x 79.3 x 70.6

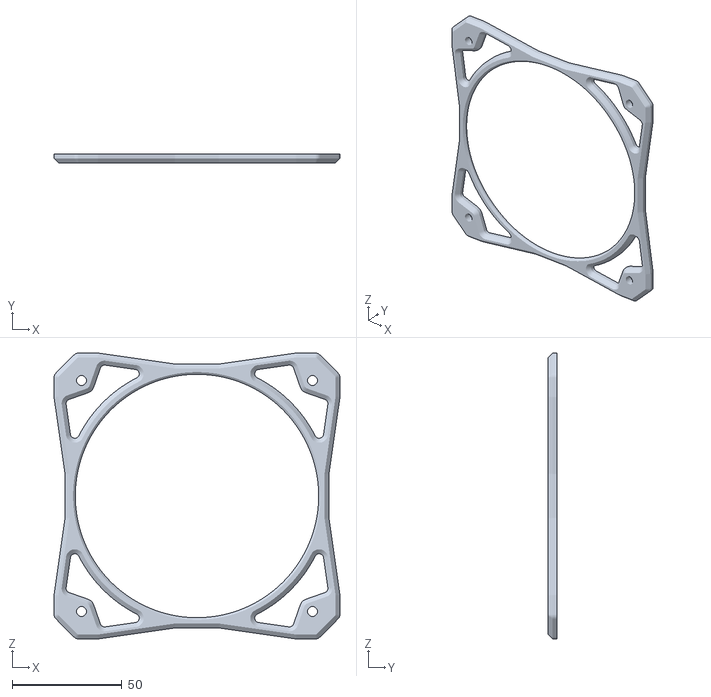
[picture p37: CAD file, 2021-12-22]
Assemblies BOM and STL/enclosure/Exhaust filter - Fume extractor/Exhaust fan guard/Exaust fan guard frame.stl
130.0 x 4.00 x 130.0

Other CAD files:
Assemblies BOM and STL/enclosure/Exhaust filter - Fume extractor/Exhaust filter housing/STLs/Exhaust fan housing.stl
Assemblies BOM and STL/enclosure/Front door hinges/logo insert.stl
Assemblies BOM and STL/enclosure/Front door latches/Locking latch/Latch top right and bottom left.stl
Assemblies BOM and STL/enclosure/Front door latches/Magnetic latch/Door latch bottom left.stl
Assemblies BOM and STL/Alignment Tools/MGN12-alignment tool.stl
Assemblies BOM and STL/Alignment Tools/MGN9-alignment tool.stl
Assemblies BOM and STL/Alignment Tools/Z Alignment Tool 12mm Rod.stl
Assemblies BOM and STL/Alignment Tools/Z Alignment Tool 8mm Rod.stl
Assemblies BOM and STL/Alignment Tools/Z Alignment tool 10mm rod.stl
Assemblies BOM and STL/Bed Assembly/STLs/Bed level adjustment knobs .stl
Assemblies BOM and STL/Bed Assembly/STLs/BedSiliconeSupport.stl
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

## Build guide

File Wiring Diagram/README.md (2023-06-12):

# PLEASE NOTE: IMPORTANT : ALWAYS CONNECT BOTH PSU DC NEGATIVE TOGETHER SO THEY HAVE THE SAME REFERENCE GROUND 
## For 48v stepstick drivers: The super 8 has 2 seperate banks of drivers. 0-2 and 3 to 7. If you want to run your Z and and E on 24v and XY on 48v, you have to use 24V on port 0-2 and place your 48v on port 3-7 for step stick driver.
## If you use the external 5160HV Pro from Mellow, then you can use the port that you want and feed 24v on both driver banks and supply 48v ONLY to the external drivers directly. 
## The new version of the External 5160HV Pro has a direct 12v Fan connection on the driver board, so no need to use a port on the Super8 for that. Connect the fans directly to the driver boards

# Useful links:
- Super8 and Super8 Pro Documation: https://teamgloomy.github.io/fly_super8_general.html
- Super8 Std Klipper info: https://mellow.klipper.cn/#/board/fly_super8/
- Super8 Pro Klipper info: https://mellow.klipper.cn/#/board/fly_super8_pro/


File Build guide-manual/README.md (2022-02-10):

# This guide is a WIP (Work In Progress).  Please make sure you consult GitHub Assembly/Bom section as well for more details

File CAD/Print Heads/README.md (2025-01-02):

The Vz-printhead has moved Repos. 
If you are looking for the Printed version: https://github.com/VzBoT3D/Vz-Printhead-Printed
If you are looking for the metal version: https://github.com/VzBoT3D/Vz-Printhead-CNC
Disclaimer: Please note that the metal parts are work of the Vzbot team. To ensure quality components and further funding of our project, we do not offer these parts as CAD files.

The Print head is a modified EVA carriage to fit the VzBoT. The EVA project is owned and maintained by Pawel. Big thanks and credits to the man behind this.
https://main.eva-3d.page/

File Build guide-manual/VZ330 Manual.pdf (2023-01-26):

# MANUAL VZ-330

## About

VZ 330 is the original VzBoT printer and has been in development since 2020. It is a High speed, moderately sized 3D-printer, based on the TronXY XS5(A) CoreXY frame, but can be easily adapted for other 2020 aluminum extrusion frames. The design is built around the popular TronXY XS5(A) but is not limited to this size, the frame can be scaled up or down to suit your own needs.

As this printer was built from modifying the TronXY you can do the same working on part by part and skipping around the guide or work through the guide and start from scratch. The entire z assembly is interchangeable, same for the partial printed printhead (exception for the front and back plate), y gantry idlers and all the smaller parts like the feet and braces. This is all aimed to make your experience as customizable as possible to truly make the printer yours.

A resent development is the fact that our friends over at mellow and f3d have started building specialized parts for VzBoT to replace 3d printed parts. This guide will try to show you how to build in both cases.

It is recommended to use the provided .step files while assembling. This manual only covers the most critical parts of the build at this moment. For using the .step files as part of the build we recommend the free version of Autodesk Fusion360, it is not hard to use and look around in the files, so even people without prior experience can do this!

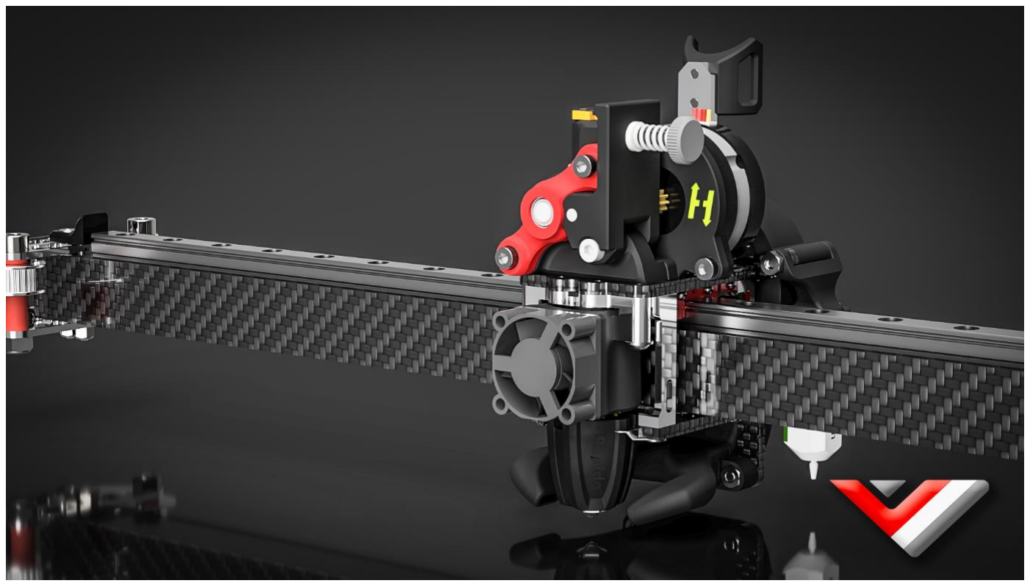
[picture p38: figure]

*Disclaimer: VzBoT is an opensource passion project, this manual is not definitive, and we try to make it as polished as possible. Fortunately, we all make errors so use common sense when following this guide. If you have any questions fortunately for you, we have a active discord full of incredibly knowledgeable people: https://discord.gg/auJrs8suVk

## Print settings:

We recommend printing all parts in ABS, ASA or similar material to be able to withstand the high heat environment in the printer enclosure.

Print settings should always be tuned for your own material and tested for decent strength and layer adhesion.

We recommend the following settings:

Layer height: 0.2mm

Layer with: 0.4 to 0.6 mm

Number of walls: 4

Infill percentage: 20% to 25 % (For moving parts you can decrease this to 15 to 20 %)

Top/bottom layers: 5

## VISIT GITHUB for additional information

Visual instructions, BOM, and STLS for all of the prints in this guide can be found on the GitHub: VzBoT-Vz330/Assemblies BOM and STL (https://github.com/VzBoT3D/VzBoT-Vz330/tree/master/Assemblies%20BOM%20and%20STL)

## General order of building:

We recommend following this order of building the printer if building from scratch:

1. Frame
2. Z assembly + Bed
3. Gantry + printhead
4. Bottom and rear panels
5. Fume extractor
6. Electronics + wiring + firmware
7. First moves and checks
8. Enclosure panels + (RSCS)
9. Trim pieces

We recommend following this order of building the printer if upgrading from a TronXY :

1. Gantry + printhead

2. Bottom and rear panels
3. Z assembly + Bed
4. Fume extractor
5. Electronics + wiring + firmware upgrades
6. Enclosure panels + (RSCS)
7. Trim pieces

## 1. Frame:

Overview:

The frame is assembled through a combination of blind joints and corner brackets. The corner brackets are to help stiffen up the frame and are optional, though we highly recommend using them on every possible corner for best results.

How to assemble a blind corner Joint:

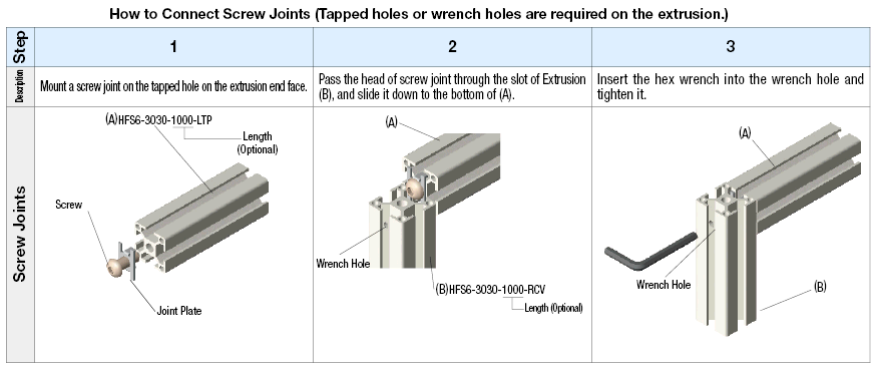
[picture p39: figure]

Useful links about the assembly of blind joints:

https://www.youtube.com/watch?v=2dvbn0rWA60

https://www.youtube.com/watch?v=ueniUWrUcjE

Bom:
Material | Quantity | Notes
M6/M5 10mm buttonhead | 16 | Depending on the type of 2020 you use you need M5 or M6 screws
530mm 2020 extrusions | 4 | Yellow
460mm 2020 extrusions | 6 | Red
530mm 2040 extrusions | 4 | Blue (all ends need to be tapped
2020 corner joints | 8
M4 T nuts | 10
M4 10mm | 2
M4 15/16mm | 8

STL files:
File name | Amount to print
Brace | 2x
Handle | 2x
Cable holder | 1x
Step 1:

To start you are going to build the 2 sides of your frame. Make sure you do your building on a nice flat surface (a stone surface is ideal if you have one available or maybe a kitchen counter. Make sure everything is as square as possible before tightening the corners. For more detail on blind joints look at the videos above. Add the optional corner braces on the bottom now.

After hand tightening you can start tightening everything down properly. Make sure every corner is exactly 90 degrees. Now you need to repeat this step a second time for the other side of the frame.

Check the two halves by laying them on top of eachother with all corners exactly in the same spot and check that every thing is parallel to between them. They need to be parallel for the printer to operate smoothly.

Step 2:

Attach the red extrusions to one side of the frame and loosely attach them you should have a upside down table now like this.

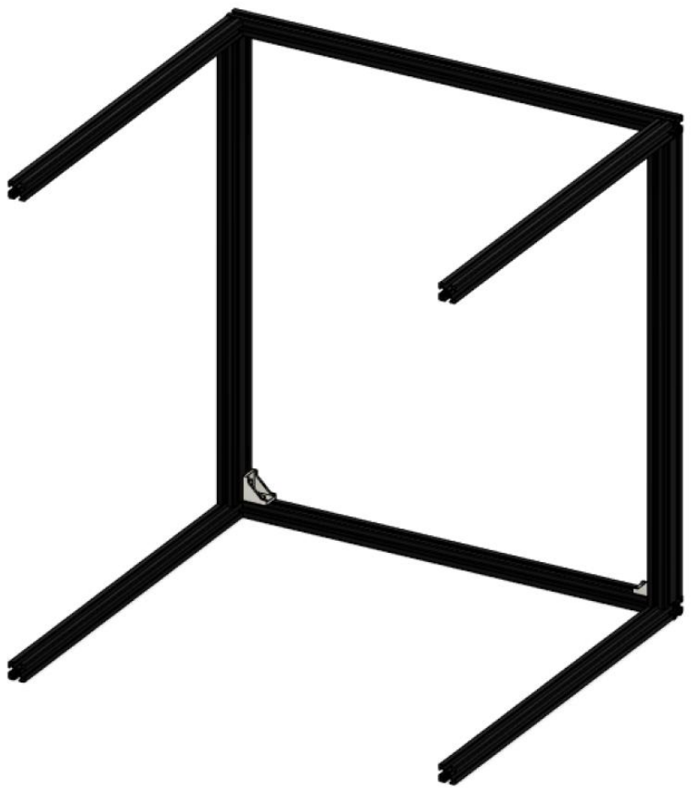
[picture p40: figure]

Step 3:

And the final side to the frame and check that everything is square one final time before properly tightening the frame. It should look something like this.

Step 4:

Attach all corner joints and check if your frame is square and strong. Now you can add the handles, brackets and cable holder.

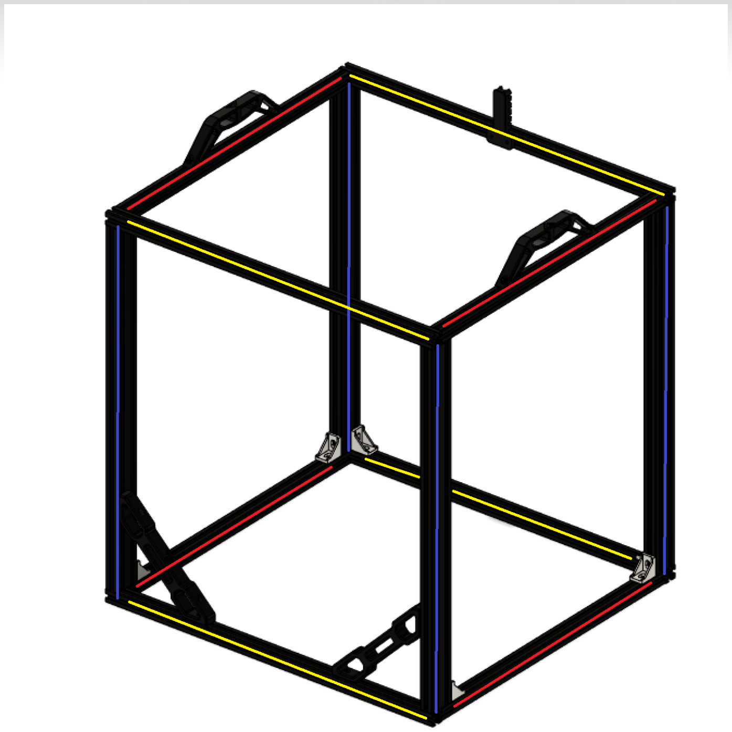
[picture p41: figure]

Congrats you have successfully built the frame to you VzBoT. This is the start of something truly impressive. This is like the foundation to your printer and is really important that it is built correctly.

## 2. Z Assembly + Bed

Overview:

The alignment procedure of the VZ330 is crucial. Make sure to check out the YouTube video explaining how to align your Z-assembly, so it is both smooth and lines up with the possible travel of the printhead.

Assembly instructions: https://youtu.be/JvF-UNoDB_I

Bom:
Material | Quantity | Notes
10mm M4 | 47
T-nut M4 | 47

15mm M3 | 24
20mm M3 | 4
M3 nut | 28
608-2rs bearing | 4
500mm leadscrew | 2
Gt2 40t 8mm pulley | 2
Nema 17 | 1
Gt2 20T pulley | 1
M3 t nut | 2
M3 30mm | 2
500mm 10mm smooth rod | 4 | Optional size, also supports 8 and 12mm as found on VZ330
Lmu10luu bearing | 4 | ^^^^
Leadscrew nut | 2
M5/M6 20mm | 2 | Depending on extrusion type
Bed springs | 6
30mm M3 countersunk | 7
M3 wing nuts | 7
M4 8mm | 1
390mm 2020 extrusion | 2
260mm 2020 extrusion | 2
2020 corner bracket | 4
M5 10mm /8mm | 8 | Depending on the 2020 corner bracket
TronXY / machined aluminum bed | 1
1100mm looped belt | 1
Microswitch | 1
M3 6mm | 4
Oldham coupler | 2 | Metal parts made by mellow

STL files:
File name | Amount to print
Z lower rod mount main | 4
Z lower rod mount clamp | 4

Z upper rod mount main | 4
Z upper rod mount clamp | 4
Single z motor bracket upper | 1
Single z motor bracket lower | 1
Lead screw upper bracket | 2
Lead screw lower bracket | 2
Limit switch mount (found in electronic section | 1
Z height adjustement screw mount | 1
Z chain mount | 1
Bearing mount | 4
Lead screw support | 2
Oldham coupler (all parts) | 2
Bed M3 support | 6
Bed alignment tool | 2
Step 1:

First assemble your bed assembly, make sure the bed frame is on a flat surface when assembling. It does take some time to get all of these aligned and square.

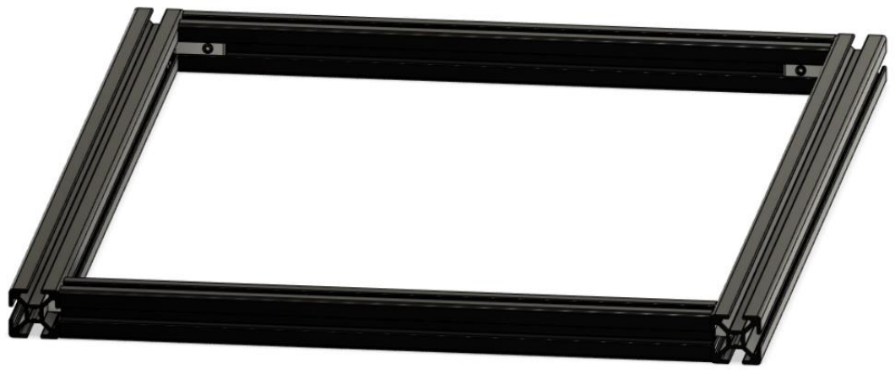
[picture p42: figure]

Next you need to insert the linear bearings in their brackets and attach them to the bed frame. It is important that the brackets line up with the inside extrusion.

Do not attach the printer bed to the frame yet!

Step 2:

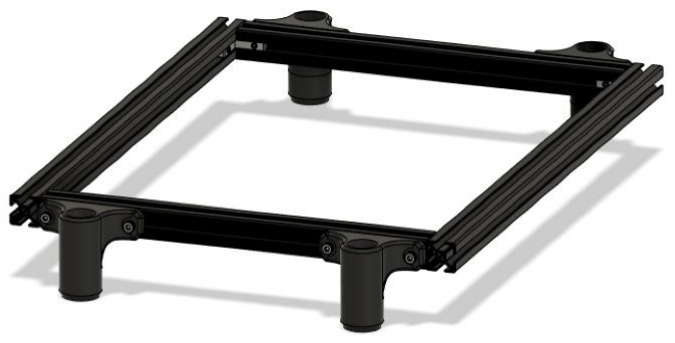
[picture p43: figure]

Attach all rod holders finger tight (upper & lower) to the frame, don’t worry about the position just yet. You want to be able to shift them around. Then insert the rods into the bearings and attach the bed frame with the rods to the respective rod holders.

Step 3:

With the assembly in place attach the two alignment tools like shown below one near the bottom, the other near the top and tighten the clamps of the rod brackets in one of the front corners. Repeat for the other side.

Step 4:

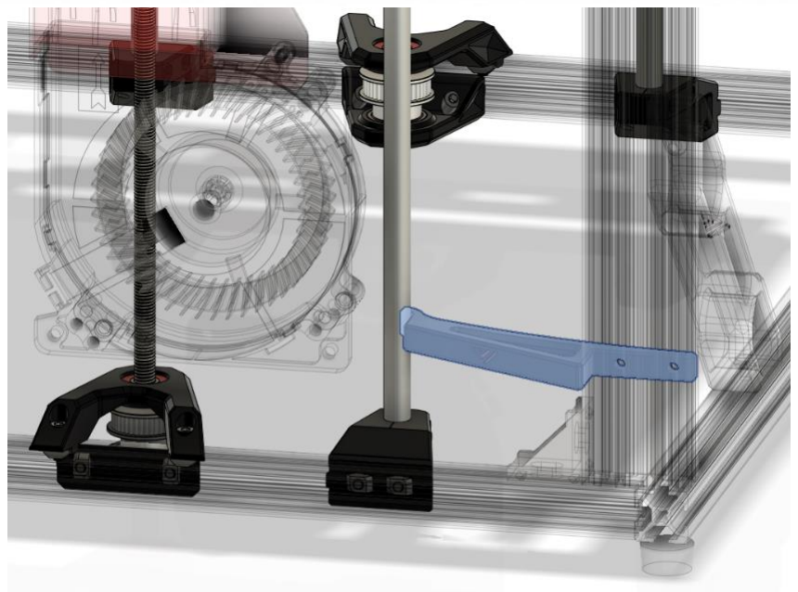
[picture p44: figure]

Once you aligned the front corners you are going to put the bed in the lowest position and wiggle the bed around. Try to get the rod pretty nice and vertical to the frame and tighten the rear bottom rod holders and tighten them to the frame.

Step 5:

Now put the bed in the highest position and tighten the clamps for the upper rods and tighten the brackets to the frame. To keep the bed up you can use zip ties or ask someone to help.

Step 6:

Insert the bearings in the leadscrew brackets (press fit) and attach the brackets like shown below. Don’t forget to put the belt around the pulley before assembling the top part of the bracket.

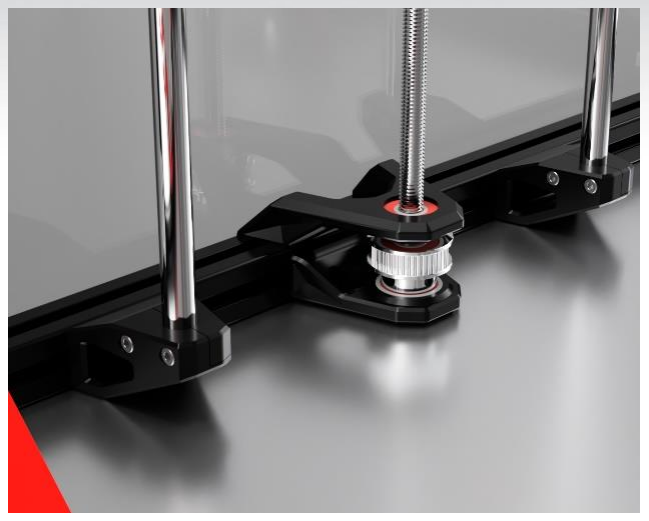
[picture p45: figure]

Then attach the leadscrew support with the oldham couplers and leadscrew nut to the bed frame and assemble the parts loosely.

Step 7:

To align the parts, measure the bracket is nicely in between the rod holders measure the distance and get it approximately centered. Turn the leadscrew a bit to help it self-align the upper leadscrew support on the bed and tighten the parts. The leadscrew should be nice and vertical. To check you can put the bed in the highest position and measure the distances between the leadscrew and z rod. The leadscrew should now be centered between both z rods.

Step 8:

Attach the single motor mount like shown below

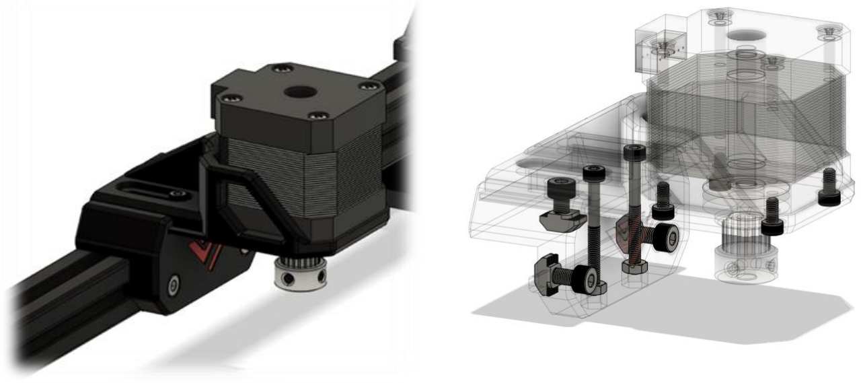
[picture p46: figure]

The top M3 screws are 30mm and lock the sliding mechanism in place. They also serve as reinforcement of the mount. Also attach the motor pulley and belt on the motor.

Step 9:

To synchronize the leadscrews, turn out the grub screws on the 40t pulleys and get the bed in the top position. Then retighten the grubscrews

Step 10:

Assemble the z switch and make sure when the bed rises the switch is triggered by the screw to avoid a bed crash at the first homing sequence.

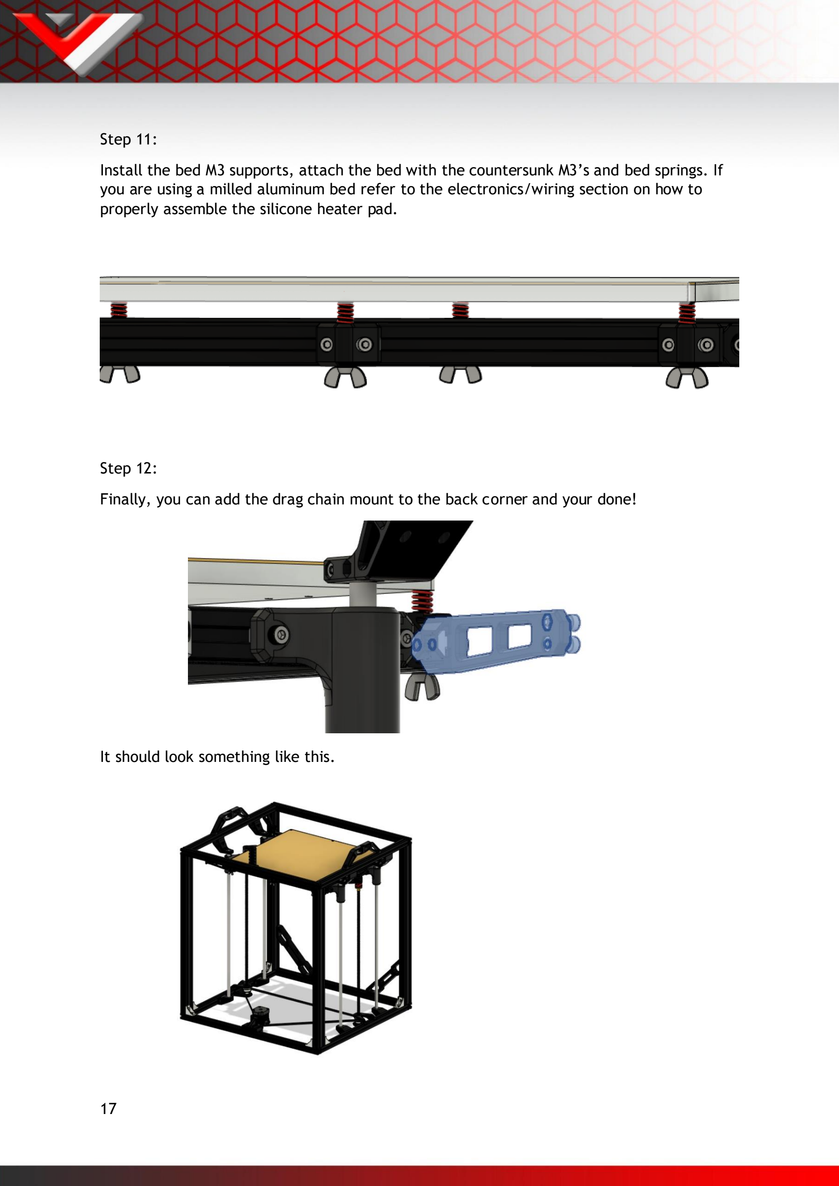
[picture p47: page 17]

Step 11:

Install the bed M3 supports, attach the bed with the countersunk M3’s and bed springs. If you are using a milled aluminum bed refer to the electronics/wiring section on how to properly assemble the silicone heater pad.

Step 12:

Finally, you can add the drag chain mount to the back corner and your done!

It should look something like this.

## 3. Gantry

Overview:

The Gantry is configurable for an aluminum version and 3d printed version. The only difference between the two configurations is the material. Construction stays the same

3.1 Motor mounts + integrated hinges

Bom:
Material | Quantity | Notes
Nema 17 motor | 2
GT 2 20 tooth pulley | 2
M4 Nut | 2
M4 nylon lock nut | 2
M4 x 12 mm washer (flat) | 2
M4 x 10mm bolt | 16
M4 x 25 or 30 set screw | 2 | Bolt can be used
M4 8mm flat head | 4
M4 T nut | 14
M3 6mm flat head | 4
M3 35mm bolt | 4

STL files:
File name | Amount to print
Motor mount Top | Left + Right
Motor mount Middle | Left + Right
Motor mount Bottom | Left + Right
Tensioner knob | 2
Knob Cap | 2
Rear frame brace or brackets from enclosure build | Left + Right

Step 1:

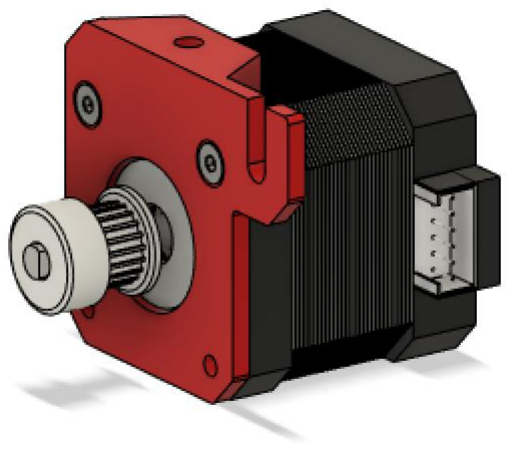
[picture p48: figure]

First attach the printed tensioner to the motor like shown above

Step 2:

Then attach the lower bracket of the motor mount to the frame.

Step 3:

Insert the M4 nut in the upper half of the motor mount and attach it on top of the lower mount and to the frame with M4 T-nuts. Don’t forget to tighten the two halves to the frame by screwing down the 40mm M4 into the printed M4 holder you inserted when assembling the frame.

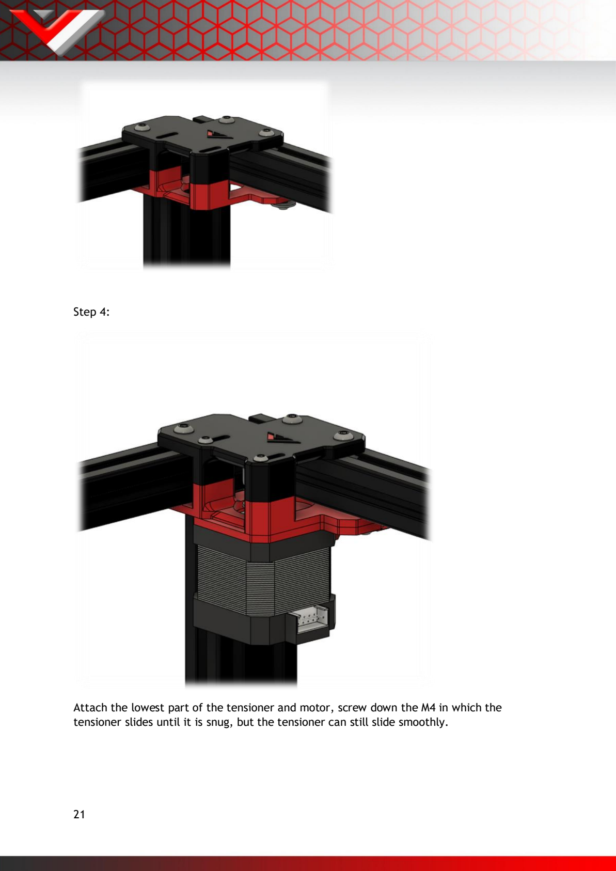
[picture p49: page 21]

Step 4:

Attach the lowest part of the tensioner and motor, screw down the M4 in which the tensioner slides until it is snug, but the tensioner can still slide smoothly.

Step 5:

Finally attach the small side panel piece and attach the front brace/integrated hinge and tensioner knob. The hinge and door assembly can also be installed now but for ease of working it is best to leave it off for now.

Step 6:

Repeat for the other side.

3.2A Front idlers

Bom:
Material | Quantity | Notes
M4 10mm bolts | 10
M4 t nuts | 10
M3 30mm bolt | 2
M5 30mm bolt | 4
20 tooth GT2 pulley | 4

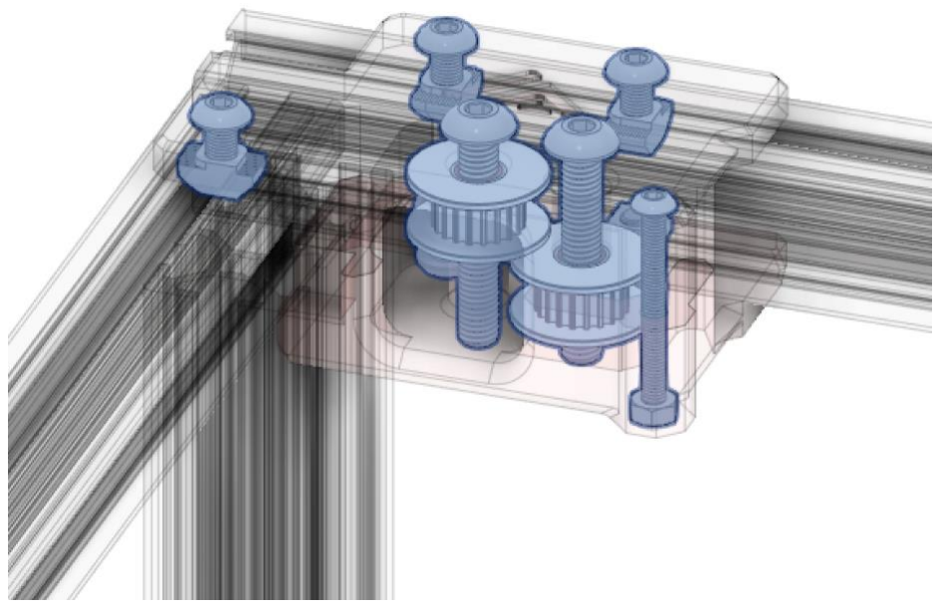
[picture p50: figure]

STL files:
File name | Amount to print
Front Idlers Mount Left BOTTOM | 1
Front Idlers Mount Left TOP | 1
Front Idlers Mount Right BOTTOM | 1
Front Idlers Mount Right TOP | 1

3.3 Printhead (printed)

The VzBoT printhead is based of EVA. The main difference is that both VZ235 and VZ330 utilize tensioners on the motor mounts, making the tensioner on the back of the printhead obsolete. As such the VzBoT EVA uses different front and back faces to keep weight low. Still the printhead can be used with the original EVA configurations for the extruder, fan duct and hotend options from EVA 2.3 and 2.4 to support all popular configurations. EVA is by default used with mgn12 rails, VzBoT is by default mgn9 so make sure you use a top part that also suits the mgn9 block.

Beware! VZ235 and VZ330 have a different belt path in regard to the printhead so the back and front plate for the printhead are not the same, use the one found in the VZ330 repository.

Also don’t forget to check the community mods section on GitHub and Discord to find more hotend and extruder configurations!

Links: https://main.eva-3d.page/

https://miragec79.github.io/HextrudORT/

3.4 Y-gantry rails, X-gantry and idlers

Bom:
Material | Quantity | Notes
MGN12H 400mm | 2
MGN9H 400mm | 1
CF square tube/aluminum tube | 1 | 2020 extrusion will also fit but is not recommended due to its excessive weight
GT2 Smooth idler | 2
GT2 toothed idler | 2
M3 8mm | 20 (or more depending on how much you use to secure the MGN12 & MGN9)
M3 T-nut | 12
M3 nut | 12
M3 10mm | 8
M3 30mm | 4
M5 30mm [titanium] | 4
M5 nut [self-locking] | 4

STL files:
File name | Amount to print
MGN12 alignment tool | 4
MGN9 alignment tool | 4
Y gantry printed bottom | 2
Y gantry printed top | 2

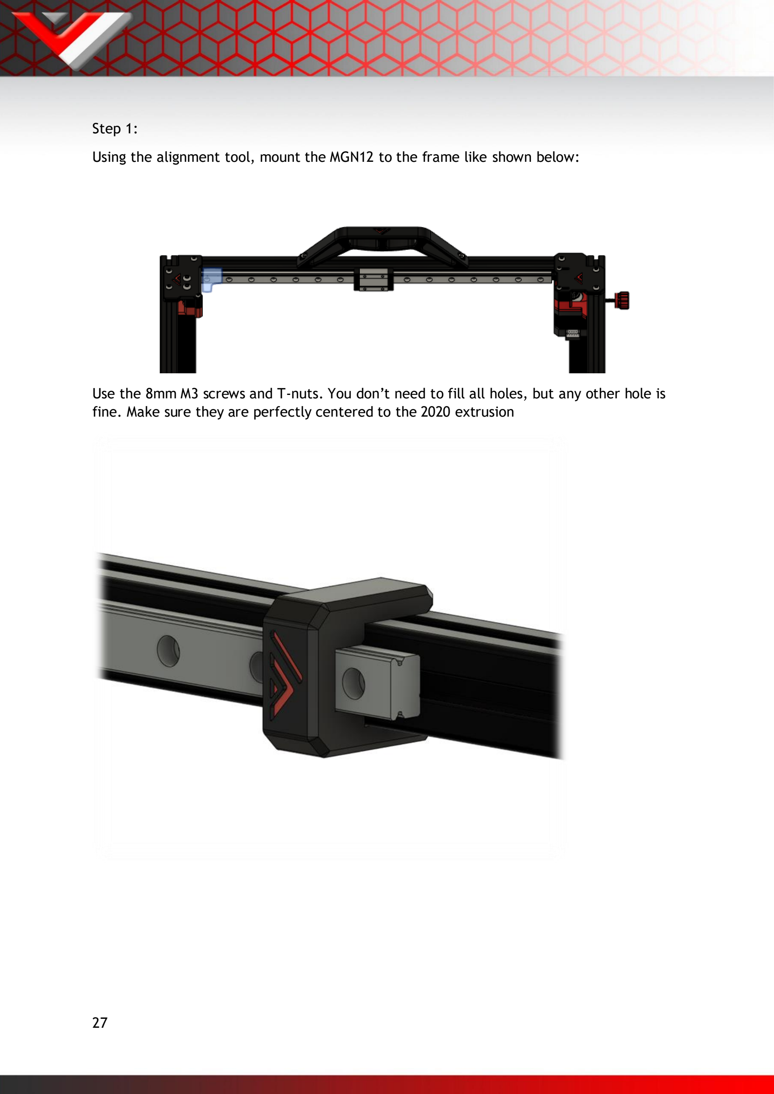
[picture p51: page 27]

Step 1:

Using the alignment tool, mount the MGN12 to the frame like shown below:

Use the 8mm M3 screws and T-nuts. You don’t need to fill all holes, but any other hole is fine. Make sure they are perfectly centered to the 2020 extrusion

Step 2:

Mount the lower half of the printed Y gantry pieces to their MGN12 cart with the 10mm M3 screws. Make sure the y gantry piece is parallel to the linear rail on both sides, you can use a small spirit level to achieve this.

Step 3:

To drill the holes in your CF-tube you’ll need to measure out where all holes will need, to do this the following is recommended: put a piece of painter’s tape on the tube, put the MGN9 on the tube with the alignment tools and have it centered. use a pencil to mark out all the holes you want to use. Put the CF-tube in your gantry and mark the holes for the tube to connect to the Y gantry, you will only need the 30mm M3 screws to secure the tube, the holes in the side are for 2020 extrusions. ( Alternately you could just buy the mellow/F3d precut version).

!warning! drilling and sawing carbon fiber is very hazardous, if you don’t buy the predrilled tube from mellow or the aluminum tube from F3D’s shop be careful. Wear protection and drill in wet surfaces!

(Please note that CF tubes dimensions can vary a bit and are not always exactly at 20mm. On the printed Y gantry, one may have to file down the printed parts a bit to fit the tube. If you use the aluminum Y gantry part, the spacing for the tube is 21mm to allow room for different CF tube size. Depending on the dimensions of your CF tube, you will have to print spacers to compensate. Please refer to https://github.com/VzBoT3D/VzBoT-Vz330/tree/master/Assemblies%20BOM%20and%20STL/Gantry/Y%20gantry/Aluminum%20Y%20Gantry (https://github.com/VzBoT3D/VzBoT-Vz330/tree/master/Assemblies%20BOM%20and%20STL/Gantry/Y%20gantry/Aluminum%20Y%20Gantry) )

Step 4:

Mount the rail on the CF-tube using the alignment tools and the 8mm M3 screws, use the M3 insert piece to hold the M3 nuts and remove this printed holder after mounting.

Step 5:

Insert the endcaps in the CF-tube and put the tube in the Y gantry brackets, add the top part of the Y gantry and their corresponding hardware. Don’t forget to add the printed X end stop part on top of the left Y gantry. Keep all hardware on this point finger tight.

Step 6:

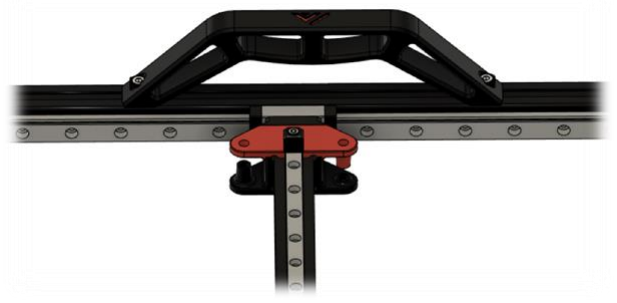
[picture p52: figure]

Insert the idlers and M5 bolts and nuts to secure, again only finger tight

Step 7:

Put the x gantry against the front idlers and tighten the Y gantry M3 hardware that hold the CF-tube in place. Then tighten the M5 hardware that hold the idlers, now your X gantry should be parallel to your rear extrusion. Measure with calipers to verify.

3.5 Belt routing and tensioning

Vz330 belt routes:

Printhead belt routing:

On the printhead’s front the belts are held in with printed clamps and M3 hardware. On the backside you need to use either tie wraps or Vz Belt clips. (Unless you use EVA with tensioner on the back)

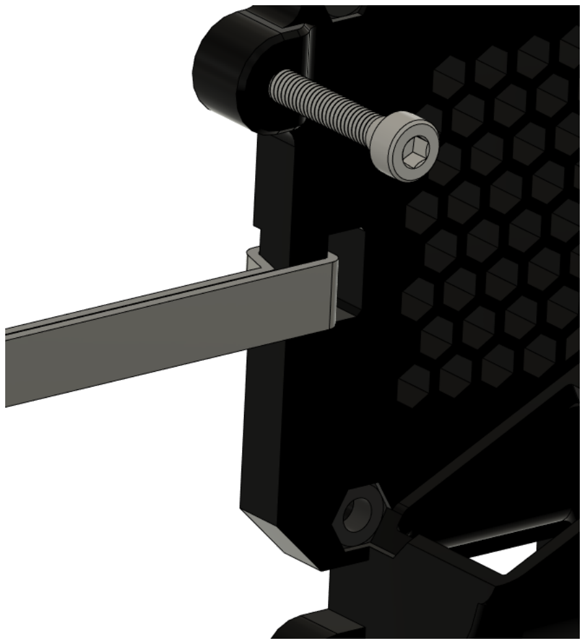
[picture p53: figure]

For the aluminum VzBoT printhead as found on https://f3d-racing-fdm.myshopify.com/ it is the same process. Refer to this guide: https://github.com/VzBoT3D/VzBoT-Vz330/tree/master/Assemblies%20BOM%20and%20STL/PrintHeads/Vz-Print%20Head%20Alu-CF/MGN9%20version (https://github.com/VzBoT3D/VzBoT-Vz330/tree/master/Assemblies%20BOM%20and%20STL/PrintHeads/Vz-Print%20Head%20Alu-CF/MGN9%20version)

Links:
VEZ3D belt tensioning: https://www.youtube.com/watch?v=qNMXW6MUV5E&t=401s

VEZ3D belt routing: https://www.youtube.com/watch?v=Ibi27Toh-pg&t=2s

3. 6 Y end stop-switch mount

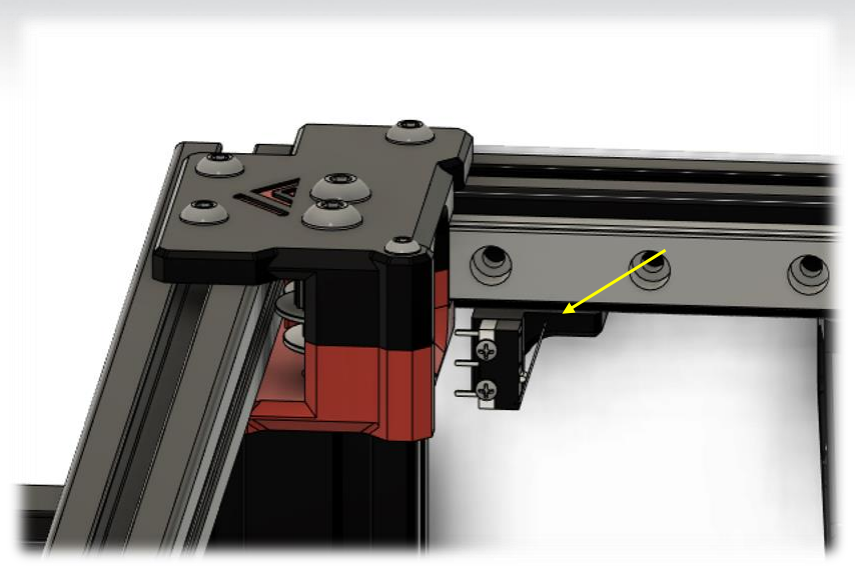
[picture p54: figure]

Bom:
Material | Quantity | Notes
Microswitch | 1
M2 10mm | 2
M4 8mm | 1
M4 T-nut | 1

STL files:
File name | Amount to print
Y switch mount | 1

## 4. Bottom and rear panels

Overview:

A full panel kit is available at F3D-racing’s shop. We recommend getting that over drilling the holes by hand because it is really difficult to get all holes in exactly the right position. If you want to drill the holes yourself, it is recommended to use the CAD as reference.

Bom:
Material | Quantity | Notes
M4/M3 6-8mm | 20* | Depending on the number of screws you use to secure your panels. Optionally you use the included enclosure trim pieces which are meant to use M3 hardware
M4 T-nuts | 24* | *
M4 20mm | 8
M5/M6 25mm | 4 | Depending on the extrusion type
Rubber foot | 4 | As found on most printers like Tronxy X5SA or Creality Ender 5(plus)
Wood screws | 8 | Optional, to screw the printer down to a surface
570x500x3 mm aluminum plate | 1 | Optionally thickness, 1.5mm also possible
530x500x3 mm aluminum plate | 1 | Optionally thickness, 1.5mm also possible

STL files:
File name | Amount to print
VzBoT Foot | 4
Foot scalable spacer (optional) | 4

Step 1:

Mount all hardware in the backpanel and put the panel on the frame. It is easiest to start tightening starting in the middle of each side and work your way outwards to prevent the panel from bulging.

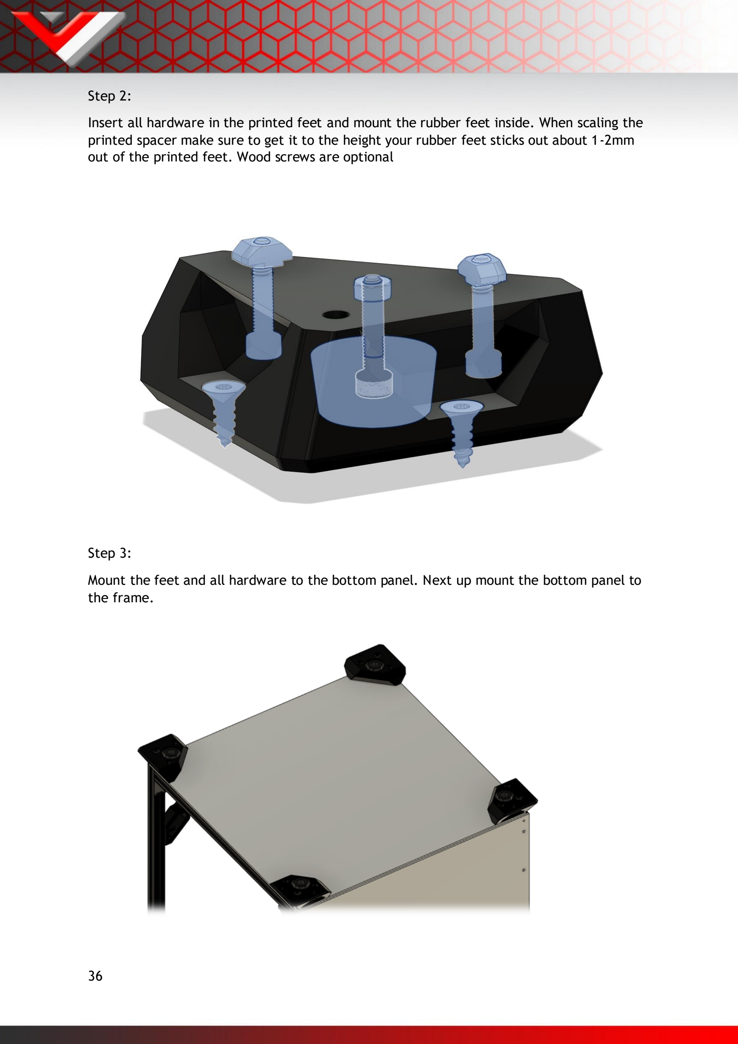
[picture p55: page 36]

Step 2:

Insert all hardware in the printed feet and mount the rubber feet inside. When scaling the printed spacer make sure to get it to the height your rubber feet sticks out about 1-2mm out of the printed feet. Wood screws are optional

Step 3:

Mount the feet and all hardware to the bottom panel. Next up mount the bottom panel to the frame.

## 5. fume extractor

Overview:

The VzBot fume extractor is an optional piece of hardware but highly recommended! This device gets rid of VOC’s (volatile organic compounds) and nasty smells that come from printing ABS filament.

Bom:
Material | Quantity | Notes
M4 50mm (button head) | 4
M3 25mm (button head) | 4
M4 nut | 4
M3 nut | 4
120x120x38mm fan | 2
HEPA filter (self-cut) | 1 | Available for kitchen applications
Activated carbon filter (self-cut) | 1

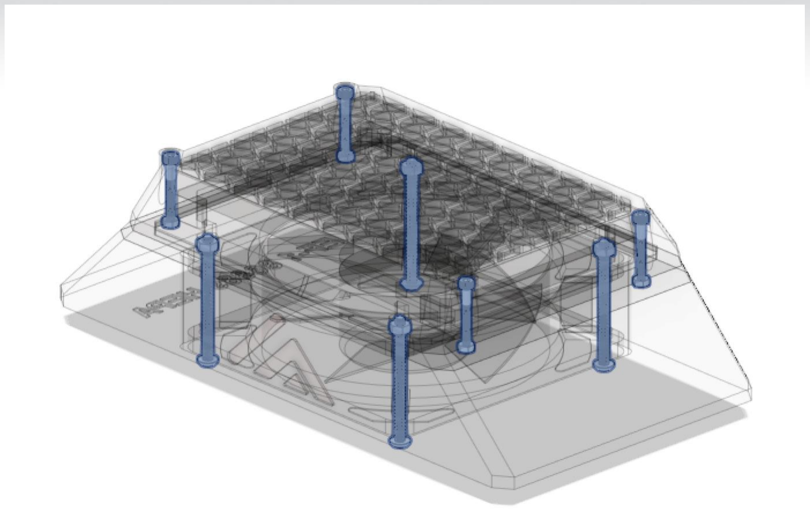
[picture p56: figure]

STL files:
File name | Amount to print
TPU grommet [optional] | 1
Fan guard | 1
Fan guard insert | 1
Exhaust fan housing | 1
HEPA holder | 1
Exhaust cover | 1

Step 1:

Start by inserting all the M4 and M3 nuts into the exhaust cover like shown below;

Step 2:

Next put the fan in the exhaust fan housing, put the fan cover on the back panel and mount the exhaust housing, exhaust cover and fans with the M4 hardware.

Step 3:

Lastly Insert you HEPA filter and activated carbon filter in the HEPA_holder and screw onto the main fume extractor housing. The activated carbon filter

## 6. Electronics + wiring + firmware

Overview:
This is a general overview of the parts recommended for a VzBoT build. Everyone is free to use their own choice of parts. STL-files for other screens etc are not natively provided and may be found in the community mod section on GitHub and Discord.

We trust everyone to use their own best judgement when wiring their printer, we do not recommend to do this without professional help if you are inexperienced in electronics.

Bom:

Material | Quantity | Notes
LED strip 310mm | 3
mainboard | 1
BTT Pi TFT50 | 1
PSU 24V | 1
PSU 48V | 1 | Optional
Wires | N.A. | Choose a correct wire gauge according to the current
C14 power switch | 1
Power chord | 1

STL files:
File name | Amount to print
LED strip bracket [print in vase mode] | 3
Power switch bracket | 1
Front screen cover | 1
Rear screen cover | 1
Screen mount | 1
Door stopper | 1

## 7. Side panels + RSCS

Overview:

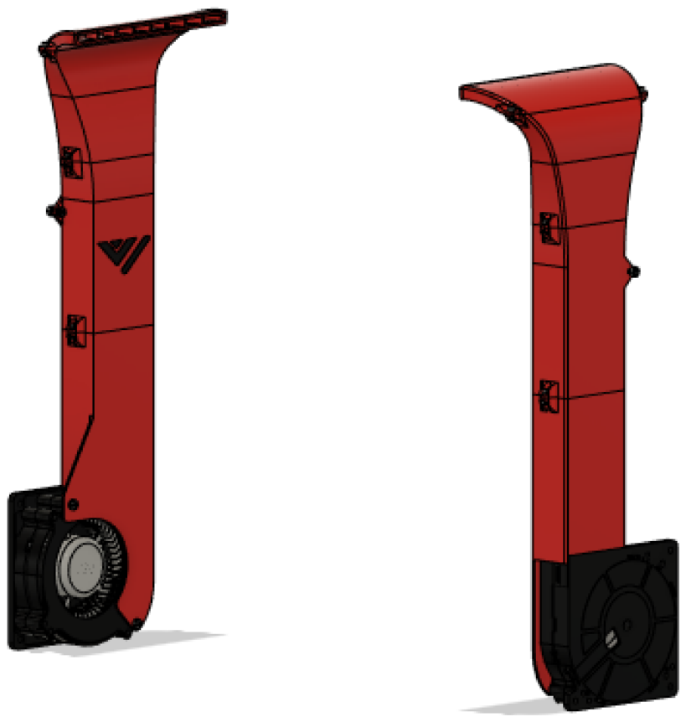
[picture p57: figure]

RSCS short for remote static cooling is an optional extra pair of cooling fans which help cool the entire print when doing unicorn speeds! RSCS is mounted to the acrylic panels and this version fits in very tight to the Z-assembly. To ensure its proper fitment it is recommended to check the CAD for accurate measurements on the hole positions.

Bom:
Material | Quantity | Notes
120mm radial fan | 2
M3 8mm | 12
M4 self tapping screw | 2 | Screw duct to fan (top screw)
M5 self tapping screw | 2 | Screw duct to fan (bottom screw)
M4 10mm | 4
M3 nut | 12

M4 nut | 4

STL files:
File name | Amount to print
Top-duct | 2
MiddleLow-duct | 2
MiddleLow duct | 2
LowerDuct | 2
Step 1: Use the M3 hardware to put the RSCS together like shown below. If the assembly won’t fit through between the 2 Z-rods. Unscrew the top part and put this on after assembly. Screw duct to 120mm fan using self tapping screws
Step 2:

Mount the RSCS to the panel. When drilling the holes make sure the duct is approximately 3-4 mm above the bed when the Z is fully homed.

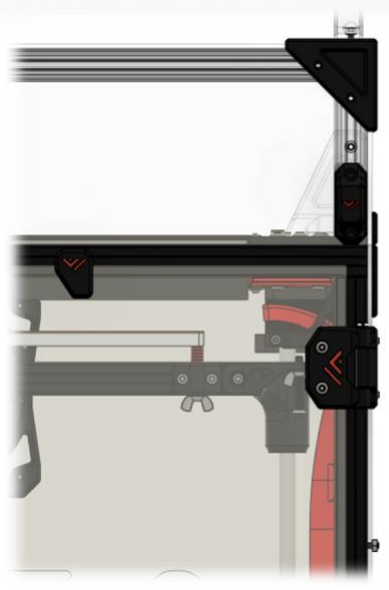
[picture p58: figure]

Step 3:

Insert the M3 hardware in the side and front (narrow) panel using the available trim pieces like shown below. When everything lines up screw everything down starting with the bolts in the middle outward. Using spring loaded tnuts is highly recommended, so they stay in place and will not fall when assembling them.

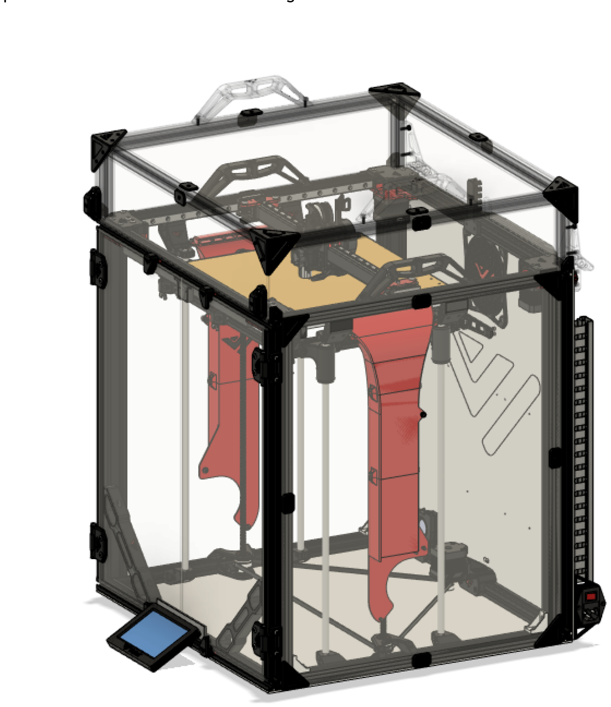
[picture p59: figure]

## 8. top cover and doors panels

Overview:

8.1 top cover & latches

Bom:
Material | Quantity | Notes
5mm X 50mm shaft | 2
M4 14mm or 15mm | 8
M4 12mm | 2 | The 2 top ones
M4 T-nut | 10

STL files:
File name | Amount to print
Left top | 1
Left middle | 1
Left bottom | 1
Right top | 1
Right middle | 1
Right bottom | 1
Step 1:

Attach both top parts to the enclosure lid if using F3ds kit there should be pre-drilled holes.

Step 2:

Attach bottom part loosely.

Step 3:

Connect the middle part on both sides to your lid with the 5mm shaft.

Step 4:

Place the lid on top of your VzBoT and slot the middle pieces in to the bottom parts and finally tighten the bottom part.

8.2 front doors hinges

Bom:
Material | Quantity | Notes
M4 50mm/4x50mm shaft | 4
M4 10mm | 16
M4 tnut | 16

STL files:
File name | Amount to print
Front door hinge part1 | 4
Front door hinge part2 | 4

Step 1:

Mount the hinges to their respective panel.

Step 2:

Put the door panels in position and insert the 40mm M4

8.3 Front door latches

IMPORTANT NOTE: Make sure to insert the frame piece before putting the side panels on!

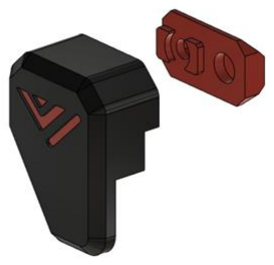
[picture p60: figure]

Bom:
Material | Quantity | Notes
M3 6mm | 4
M3 10mm | 4
M3 nut | 8
2x5mm magnet | 8

STL files:
File name | Amount to print
Latch LD | 1
Latch RD | 1
Latch UL | 1
Latch UR | 1
Latch frame side | 4
Step 1:

Insert the 2x5mm magnet in the latches, they are press fit. If not tight use super glue to hold them in.

Step 2:

Insert the M3 nuts in the latches

Step 3:

Screw the latches to the door panels using the M3 buttonheads

Step 4:

Untighten the set screws in the frame side latches and line them up with the latches, then to lock them tighten the M3 screw.

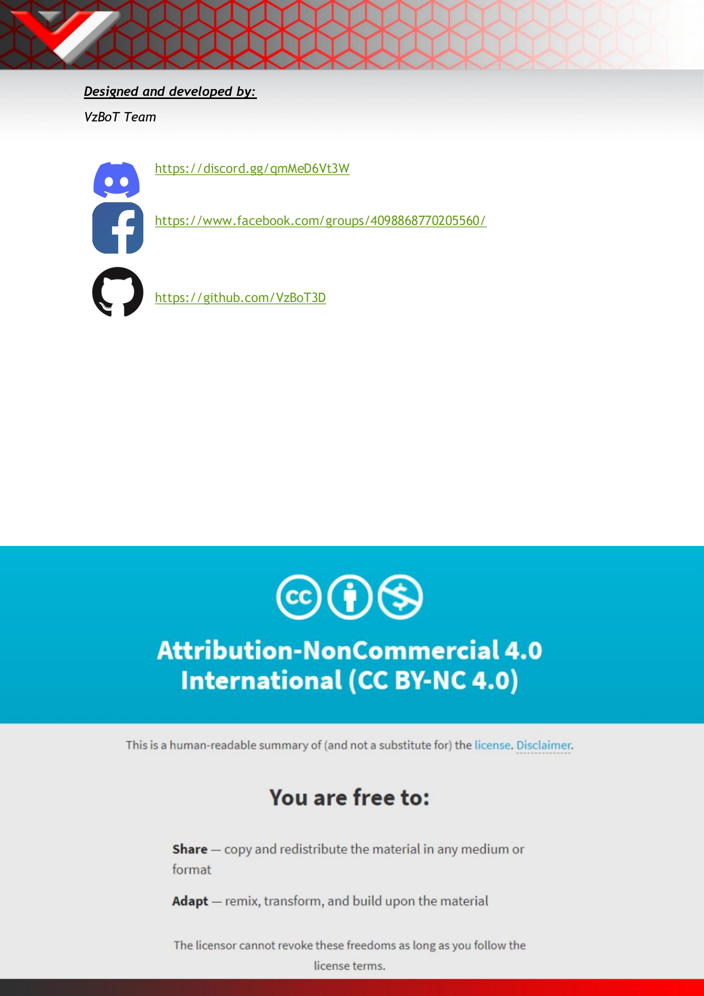
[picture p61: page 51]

Designed and developed by:

VzBoT Team

https://discord.gg/qmMeD6Vt3W

https://www.facebook.com/groups/4098868770205560/

https://github.com/VzBoT3D

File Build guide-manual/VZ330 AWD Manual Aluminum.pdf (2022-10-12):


## About

This manual is intended for the aluminum parts for VZ330 as sold by F3D-Racing and Mellow. The aluminum parts are interchangeable with the printed parts, some additional hardware is required when purchasing the motor mounts and idler mounts. Furthermore some printed parts are required in order to mount your new sexy parts!

Beware, VZ330 was never designed around AWD like VZ235. Because of this the design team was left with the frame as constraint. Due to which it was not possible to have a design that did not limit y travel for the VZ330 printhead. There is a 10mm loss in Y travel coming from 330mm.


https://f3d-racing-fdm.myshopify.com/collections/vzbot-vz330

https://mellow.nl.aliexpress.com/store/1531088?spm=a2g0o.detail.1000007.1.67f7726dJR pvIK\ (https://mellow.nl.aliexpress.com/store/1531088?spm=a2g0o.detail.1000007.1.67f7726dJRpvIK/)

*Disclaimer: VzBoT is an opensource passion project, this manual is not definitive, and we try to make it as polished as possible. Fortunately, we all make errors so use common sense when following this guide.

## Print settings:

We recommend printing all parts in ABS, ASA or similar material to be able to withstand the high heat environment in the printer enclosure.

Print settings should always be tuned for your own material and tested for decent strength and layer adhesion.

We recommend the following settings:

For non-moving parts:

Layer height: 0.2mm

Layer with: 0.4 to 0.6 mm

Number of walls: 4

Infill percentage: 40 to 50 %

Top/bottom layers: 5

For moving parts:

Layer height: 0.2mm

Layer with: 0.4 to 0.6 mm

Number of walls: 4

Infill percentage: 30 to 40 % depending on your material

Top/bottom layers: 5

## AWD Motormounts/Idlers


Bom:

Material | Quantity | Notes
M3 30mm | 2
M3 6mm buttonhead | 6 | Buttonhead is required, barrelhead will not fit
M4 10mm | 10 | +2 for mellow version
M4 T-nut | 10
Shoulder bolt 5mmx20mm [M3] | 4 | M3 threading with 6mm of threaded length, if longer grind down the ends. Correct shoulder bolts available at mellow & F3D
GT2 Toothed idler | 2
Gt2 Smooth idler | 2
GT2 motor pulley | 2

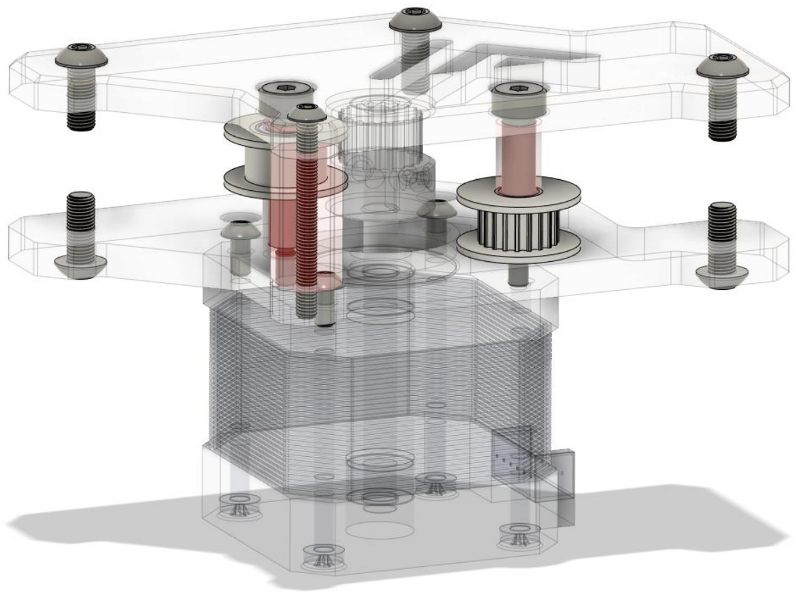
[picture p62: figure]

STL files:

File name | Amount to print
Spacer long | 4
Spacer short bottom | 2
Spacer short top | 2
Spacer M3 corner | 2

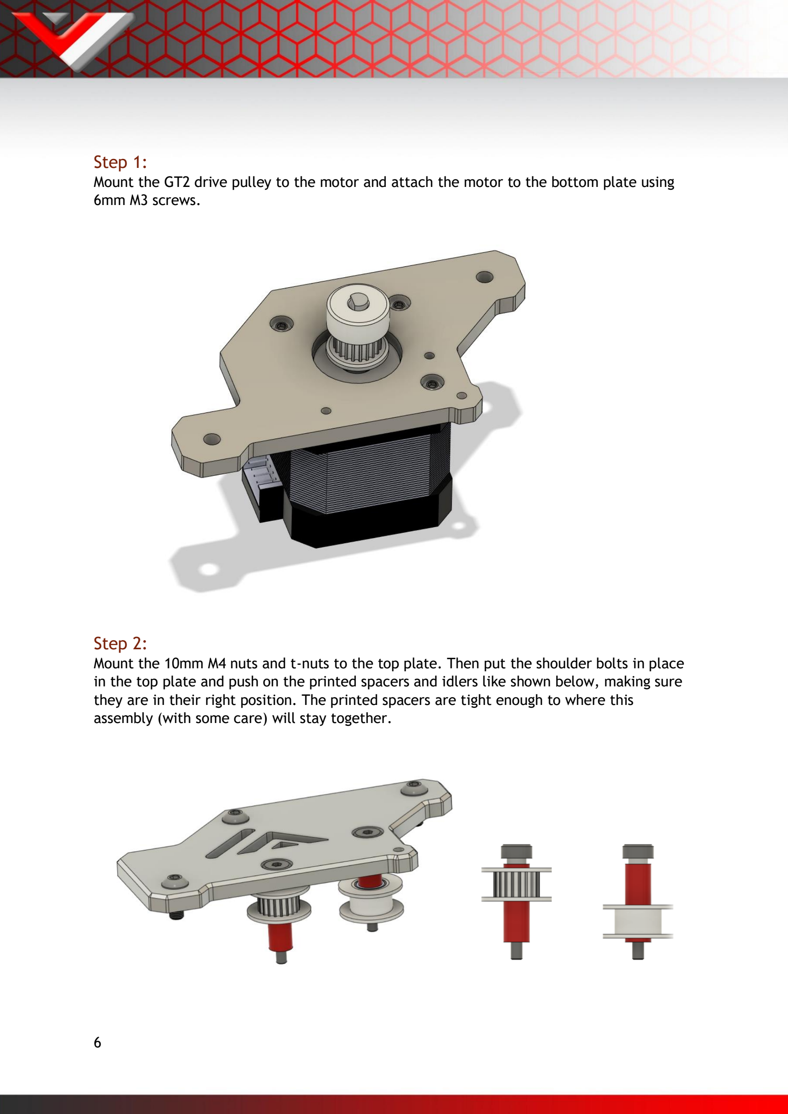
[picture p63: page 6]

Step 1:
Mount the GT2 drive pulley to the motor and attach the motor to the bottom plate using 6mm M3 screws.
Step 2:
Mount the 10mm M4 nuts and t-nuts to the top plate. Then put the shoulder bolts in place in the top plate and push on the printed spacers and idlers like shown below, making sure they are in their right position. The printed spacers are tight enough to where this assembly (with some care) will stay together.

Step 3:
Attach the bottom assembly to the printer frame using 10mm M4 screws and t-nuts. After this attach the top assembly from the previous step loosely. Make sure the shoulder bolts thread before tightening all screws.

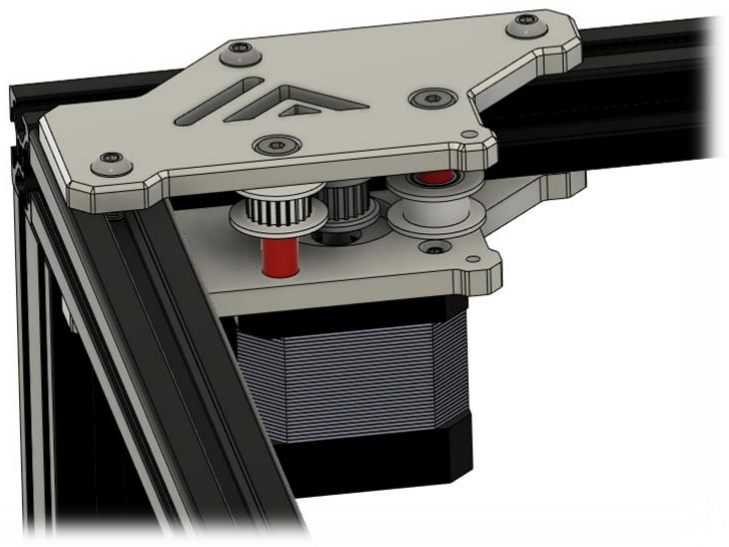
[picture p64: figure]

Step 4:
Insert the printed corner spacer and install the 30mm M3 like shown below.

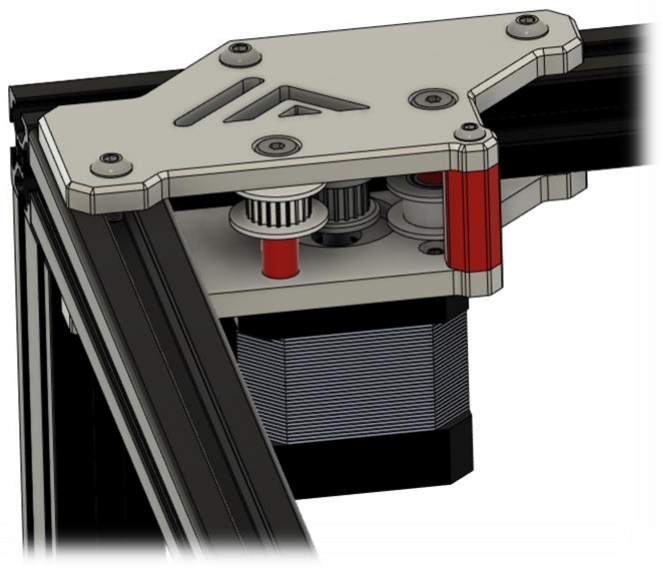
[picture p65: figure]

Step 5:
Repeat the same process for the other side making sure to put the idlers in their correct position.

## Firmware:

Klipper, RRF and Marlin natively support AWD for Corexy kinematics. For a Klipper example Cfg suited for AWD check the VZ235 Github page.

https://github.com/VzBoT3D/VzBoT-Vz235/tree/main/Firmware

XY motion Example CFG Klipper:
[stepper_y]

step_pin: PE11

dir_pin: !PE10

enable_pin: !PE9

rotation_distance: 40

microsteps: 16

full_steps_per_rotation: 200

endstop_pin: ^PB13

position_endstop: 0

position_max: 235

homing_speed: 25

homing_retract_dist: 0

[tmc5160 stepper_y]

spi_bus: spi4

cs_pin: PE7

interpolate: false

#diag1_pin: PB14

run_current: 1.6

[stepper_y1]

dir_pin: !PC13

enable_pin: !PE5

step_pin: PE6

rotation_distance: 40

microsteps: 16

full_steps_per_rotation: 200

[tmc5160 stepper_y1]

spi_bus: spi4

cs_pin: PC14

interpolate: false

#diag1_pin: PB14

run_current: 1.6

[stepper_x]

step_pin: PD8

dir_pin: !PB12

enable_pin: !PD9

rotation_distance: 40

microsteps: 16

full_steps_per_rotation: 200

endstop_pin: ^PB14

position_endstop: 0

position_max: 235

homing_speed: 25

homing_retract_dist: 0

[tmc5160 stepper_x]

spi_bus: spi4

cs_pin: PE15

#diag1_pin: PB13

interpolate: false

run_current: 1.6

[stepper_x1]

dir_pin: !PE4

enable_pin: !PE3

step_pin: PE2

rotation_distance: 40

microsteps: 16

full_steps_per_rotation: 200

[tmc5160 stepper_x1]

spi_bus: spi4

cs_pin: PC15

interpolate: false

#diag1_pin: PB14

run_current: 1.6

## Setup and tuning:

After finishing the build one must take care to properly set up the AWD system. It is important to “sync the motors”. In order to achieve this it is advised to use the following macro’s in klipper:

[gcode_macro enable_stepper]

gcode:

SET_STEPPER_ENABLE STEPPER=stepper_x ENABLE=1

SET_STEPPER_ENABLE STEPPER=stepper_x1 ENABLE=1

SET_STEPPER_ENABLE STEPPER=stepper_y ENABLE=1

SET_STEPPER_ENABLE STEPPER=stepper_y1 ENABLE=1

[gcode_macro disable-steppers]

gcode:

m84


Step 1:
Set belt tension like on a normal 2WD VZ330.
Step 2:
Loosen the grubscrews on one of each set of motors, make sure the grub screws will not be on the flat side of the stepper shaft.
Step 3:
Boot up the printer and order “enable stepper”.
Step 4:
Tighten the stepper grub screws and disable steppers again.


Designed and developed by:

The VzBot Team

https://discord.gg/qmMeD6Vt3W

https://www.facebook.com/groups/4098868770205560/

https://github.com/VzBoT3D



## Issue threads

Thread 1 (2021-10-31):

Y-Stop mount missing switch mounting holes

mobilemcclintic, 2021-10-31:
Y-Stop mount is missing the holes to mount the switch.  It's not easy to see in the full step file because the screws are there.  If you hide them, the mounting surface is solid.

simonvez, 2022-01-08:
Thanks for reporting will fix that in CU4

simonvez, 2022-01-08:
new STL have been uploaded and CAD has been fixed for CU4 release

Closed 2022-01-08.

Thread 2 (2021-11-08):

Power supply 48V

demonlibra, 2021-11-08:
Motor Wantai 42BYGHW811
Rate voltage 3.1V
Rate current 2.5A

Maximum power dissipation for this motor 3.1V x 2.5A = 7.75W
Two motors 7.75W x 2 = 15.5W

Why you preffer power supply 350W 48V?

HoshuaK, 2021-11-19:
I believe he's running the stock Tronxy bed which runs on 24V.

demonlibra, 2021-11-19:
I write about power supply 48V which using only for stepper motors.

mouamart, 2021-12-26:
> I write about power supply 48V which using only for stepper motors.

I believe it's to power the TMC5160HV driver's not the stepper motor directly

demonlibra, 2021-12-26:
Just think about it.
I am sure you can use a power supply with a much lower power, for example, 50 watts.
Of course this requires real testing.

mouamart, 2021-12-26:
> Just think about it. I am sure you can use a power supply with a much lower power, for example, 50 watts. This will be a threefold power reserve. Of course this requires real testing.
You're stepper motor problem don't need the 48v psu but the 48v system is for the ODrive motor

https://youtu.be/1XzD7lGNaek

demonlibra, 2021-12-26:
I thought you were using 48V for stepper motors.
https://www.youtube.com/watch?v=B0E0zaYVU94

tehmaze, 2021-12-27:
For motor power budget use the formula on the Watterott wiki: https://learn.watterott.com/silentstepstick/faq/#what-power-supply-do-i-need

Closed 2022-01-06.

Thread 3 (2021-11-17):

Z stop that hands off bed

coilboii, 2021-11-17:
Is there a stl for the hindge that hangs off the side of the bed with the screw sticking up to hit the z stop or is there a item you used. Nothing in the bom nor the stl

coilboii, 2021-11-17:
Supposed to say hangs off

simonvez, 2022-01-06:
here mate : https://github.com/VzBoT3D/VzBoT/blob/master/Assemblies%20BOM%20and%20STL/Bed%20Assembly/STLs/Z%20height%20adjustement%20screw%20mount.stl

simonvez, 2022-01-06:
if you want to test the new one coming in CU4... I can share you the files now ?

simonvez, 2022-01-06:
[Z switch mount.zip](https://github.com/VzBoT3D/VzBoT/files/7824916/Z.switch.mount.zip)

here you can test it

simonvez, 2022-01-06:
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

Closed 2022-01-08.

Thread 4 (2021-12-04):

BOM

goosst, 2021-12-04:
Interesting project!
This might not be the best place to ask but:
- I understand there is a BOM on this github site / google drive. To make a cost estimate however, it's not clear which parts of this BOM are reused from the tronxy and which need to be upgraded / get thrown away from the tronxy. Is it fair to assume that all extrusions, lead screws, stepper motors, heated bed and support are reused in this build?
   - Or even better, could it be added to a column in the BOM what is new and what is original to the tronxy?

- any advice where to start? Are there some guides out there or is it just going based on the CAD files?

thanks!

mouamart, 2021-12-26:
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
It's in the spreadsheet on top. If it say necessary buy it means this part is not included with tronxy x5sa kit ,  optional buy  Means either the part is included but not very good quality or the features is optional for both new build or tronxy x5sa upgrade. None that means this part is included with tronxy x5sa kit.
Hope that helps

goosst, 2021-12-28:
thanks!
or I was blind or it has been added since I opened the ticket :)

Closed 2021-12-28.

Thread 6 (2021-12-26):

Firmware for the build

mouamart, 2021-12-26:
A lots us not to familiar with firmware compiles. Is there going to be a firmware ready to use or a step by step on how to install the firmware for vzbot??..

simonvez, 2022-01-08:
It is a bit hard to provide this. I can provide my klipper config, but its based on my printer. Not everyone runs the same board, drivers, electronics.. so it is very hard to provide all the information. I can however provide what I run if you wish

mouamart, 2022-01-08:
> It is a bit hard to provide this. I can provide my klipper config, but its based on my printer. Not everyone runs the same board, drivers, electronics.. so it is very hard to provide all the information. I can however provide what I run if you wish

Just provide firmware based on BOM and if you know some good YouTube videos and documentation as a reference that would be a bonus

karlspena, 2022-01-08:
Please do

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

thantik, 2022-01-16:
A klipper config would certainly be a huge jump in progress when I get to that point.  I'm still waiting on my parts from Mellow (CF tube and alum brackets), but I've got the Mellow Super 8 board, and basically the exact same configuration.  Lots of boards actually route a lot of the same wires, so a klipper config will probably even match up with most other boards with the same processor - or at least is a good jumping-off point to modify to fit an existing board.  Macros and such that you're using also give people sane parameters to aim for in order to replicate your work.

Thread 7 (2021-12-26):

Electronic

mouamart, 2021-12-26:
your using mellow super 8 motherboard as an official board for the build, raspberry pi 3, pitft50, 8 bar relays ext. Can you add wiring diagrams and instructions on how to wire everything together. Thanks in advance

simonvez, 2022-01-08:
the 8bar relay is no longer used in my case since the Super8 has enough fan outputs for our needs.  The wiring is pretty straight forward for the rest.  The Pitft50 is wired with a 1m ribbon cable for pi

mouamart, 2022-01-08:
> the 8bar relay is no longer used in my case since the Super8 has enough fan outputs for our needs. The wiring is pretty straight forward for the rest. The Pitft50 is wired with a 1m ribbon cable for pi

Then probably you should remove it from the bom as I did purchase it based on the bom list.
I do understand it's straight forward and probably won't take me much to figure it out but a wiring diagram based on the BOM would b helpful for a lots of people as lots of people don't know how to wire a thing without instruction.

simonvez, 2022-01-26:
yes I need to work on this too

simonvez, 2022-01-26:
I will make the relay optional for those running smaller boards

simonvez, 2022-04-11:
Thanks a ton Mouamart!!!

Closed 2022-04-11.

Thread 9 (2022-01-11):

wanting to adapt to x5sa 400+ models

naruhaxor, 2022-01-11:
what all would be need for an adaptation to the 400 models of the X5sa? i am currently trying to ompile a buy list (i am basically having to (de) pro mine to get rid of the tronxy linear rails but i like where this is going and would also like to possible offer my assistance in creating adaptations to the larger tronxy core xy printers

chrishenze, 2022-01-11:
This answer is on the guess that the frame of the x5sa with 400mm travel is just 70 mm wider than the normal (pls recheck)

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

So you would need a longer cf tube with 510mm, but a normal 500mm should also work and would be easier to source.
2x MGN12H in 450mm should also barely fit the travel, as well as 450mm MGN9H

naruhaxor, 2022-01-11:
So if I end up just getting the 500 mm extrusion do you have the step files
for the XY carriages that allows it to attach to the sides of the printer
so that way I can adjust if necessary

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

chrishenze, 2022-01-13:
There is only one printed version of the gantry part. I checked the CAD model and 5 mm shorther on each side might not work, you would have to cut a semicircle ouf ot the cf tube:
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

Closed 2025-01-02.

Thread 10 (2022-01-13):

printed motor mounts

LonyB, 2022-01-13:
Printed motor mounts 3D top images do not fit bottoms, holes do not line up. No hole where there should be one. Images do not match causing confusion. Appears to be an Older .stl

chrishenze, 2022-01-13:
I rechecked the STL models and couldn't find what you are meaning. Could you upload a screenshot?

LonyB, 2022-01-14:
Looks like I have it figured out, I downloaded one set of .stl files for the bottom then the tops later after the revisions so thats why they didn't match up. but stl doesn't match the 3d view in the folder or at least that's how it was earlier today.

Closed 2022-01-16.

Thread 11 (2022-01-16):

Oldham Coupler

psusong, 2022-01-16:
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

chrishenze, 2022-01-16:
These are the oldham couplers and currently you need to print, sand and lube them to get them working. Mellow should make them in the long run.

psusong, 2022-01-17:
I was printing him and saw in the video there was new copper.
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

karlspena, 2022-01-17:
Where can we get the brass oldham couplers?

chrishenze, 2022-01-17:
The oldham coupler on the picture is a prototype from Mellow, they will probably sell them in the future.

chrishenze, 2022-01-17:
I added the STLs of the oldham coupler for easier printing.

chrishenze, 2022-01-20:
They are now available from Mellow: https://s.click.aliexpress.com/e/_ASAMpS

Closed 2022-01-24.

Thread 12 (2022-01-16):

External Mount Nema23 for 0,9° Step Angle

FLXMM, 2022-01-16:
Is it possible to provide the CAD (Fusion360) files for the external Nema23 Mounts?
As far as I can see they are ment for 1,8° Step angle Nema23 because of the 2:1 (40T pulley) which isnt necessary with these LDO Motors LDO-57STH41-2804MAC(HEV) (made for the HevORT).

I'd like to rework the design so no extra pulley is needed. Or might there already be one in the works?

FLXMM, 2022-01-16:
Ok after looking at it more closely: I guess the easiest solution for now would be just swap the 40T for a 20T pulley..

FLXMM, 2022-01-16:
Ok so after going through the BOM I saw its mentioned anyway. SO well best example  of read first...

Closed 2022-01-16.

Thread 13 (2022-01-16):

Wiki - Motors (Stepper)

FLXMM, 2022-01-16:
Didnt know where to mention this. Hope hear is right.

The mentioned data in the Motors table for the E3D High Torque Nema17 is wrong. And the Units for Inductance and Ampere are switched!

https://e3d-online.zendesk.com/hc/en-us/article_attachments/360016686858/High_Torque_Motor.pdf

E3D High Torque
Inductance : 2.8mH (instead of 2.8A)
Ampere : 1.68A (instead of 2.8mH)

simonvez, 2022-01-24:
corrected thanks !

Closed 2022-01-24.

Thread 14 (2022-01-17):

about pei？

psusong, 2022-01-17:
Hello, can you see how you dealt with the pei, whether it is the magnet placed behind the aluminum plate or the magnetic surface directly attached

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

chrishenze, 2022-01-17:
The magnetic sheet should be directly put on the heated bed.

psusong, 2022-01-19:
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
I see that some people do this. I don't know if it will be deformed. If the magnetic film is directly attached, will it be uneven?

chrishenze, 2022-01-22:
You don't need a magnetic sheet if you already have magnets in your bed. You would just put the spring steel plate with the PEI layer on it.

Closed 2022-01-25.

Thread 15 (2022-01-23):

Provide CAD Nema23 Motor mount

FLXMM, 2022-01-23:
Hi could you plz provide the .step file for the nema23 Motor mount so i can make a belt tension option similar to the nema17 mount for the vz printhead.

simonvez, 2022-01-24:
sure.. but I only have the one with the motor on the side. I think motor has to remain on the side, while there is the same mechanism on the back to pull on the pulleys. And use the same thensioning method with the same hole in the back, and same top cover hinges or brackets

https://github.com/VzBoT3D/VzBoT-Vz330/tree/master/CAD/Gantry/Motor%20Mounts/ODrive-Nema23

FLXMM, 2022-01-24:
Hi thx... i thought about making a mechanism that moves the whole 10mm shaft including both bearings.
But that might over complicate the design... alternativly i thought about editing the existing tensioning mount and just put the Nema23 upside down on top and tension it that way. that would also get rid of the closed belt, bearings etc. BUT that would mean you cant use the existing top cover, since the motor will "block" the corner. Any thoughts?

Closed 2022-01-24.

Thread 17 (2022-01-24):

The back plate with no tensioner.stl is not suitable for new EVA 2.4.2 models

arieslight, 2022-01-24:
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

carloshespanhol, 2022-01-24:
I am planing to use this part and have the same problem

simonvez, 2022-01-24:
we will provide one . There is already one if you look in the pull request. A member has made one. We will review it and publish it if it is good

carloshespanhol, 2022-01-25:
In the pull request I found one with tensioner, I' m looking for the back without tensioner.

arieslight, 2022-01-25:
yeah, In the pull request there is no one without tensioner. I modified one without tensioner but it's not perfect

arieslight, 2022-01-25:
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

arieslight, 2022-01-25:
[plate with no tensioner（beta by arieslight）.zip](https://github.com/VzBoT3D/VzBoT-Vz330/files/7934921/plate.with.no.tensioner.beta.by.arieslight.zip)
it is not perfect,but If you can't wait for the official release，you can try it

carloshespanhol, 2022-01-25:
Thank you

Closed 2022-01-25.

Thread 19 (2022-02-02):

BOM for the aluminum front idler

mouamart, 2022-02-02:
there is no BOM for the aluminum front idler. just ordered my kit from mellow I hope I can get the BOM for the aluminum front idler before they arrive. thanks and a Tim Hortense coffee on the way to u ;)

simonvez, 2022-02-07:
https://github.com/VzBoT3D/VzBoT-Vz330/tree/master/Assemblies%20BOM%20and%20STL/Gantry/Front%20Idler%20mounts/Aluminum/BOM

Closed 2022-02-07.

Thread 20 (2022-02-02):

BOM for single Z motor mount is missing 4 screws

Polar-Ted, 2022-02-02:
https://github.com/VzBoT3D/VzBoT-Vz330/tree/master/Assemblies%20BOM%20and%20STL/Z%20assembly/Single%20Motor%20Mount/BOM

The 4 M3x10mm screws to mount the motor are missing from the BOM for the mount.

simonvez, 2022-02-07:
thanks ! I will add them

Closed 2022-02-07.

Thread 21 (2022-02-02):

Vz-HextrudrORT - STLs vs CAD

FLXMM, 2022-02-02:
Hi the BOM and STLs differ from the
https://github.com/VzBoT3D/VzBoT-Vz330/blob/master/CAD/Vz-HextrudORT/Vz-Hextrudort-Low%20motor.step
there is an additional screw on the bottom right of the main body and the backplate in the CAD file but not in the STLs

Closed 2022-02-07.

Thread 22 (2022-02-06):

klicky probe？

psusong, 2022-02-06:
Can add support for klicky probe? Works great on Voron.
thank

psusong, 2022-02-06:
https://github.com/jlas1/Klicky-Probe

simonvez, 2022-02-07:
Hi, are you requesting the support for the EVA or the Vz-Printhead ?

psusong, 2022-02-26:
My machine has not been installed, and when it is installed, I will study

hschraep, 2022-03-24:
i would preffer it for both heads.

psusong, 2022-03-30:
[SSerpenteSS](https://github.com/SSerpenteSS) Make a fork of vzbot

https://github.com/jlas1/Klicky-Probe/pull/69

jlas1, 2022-05-07:
Done, published

Closed 2022-06-13.

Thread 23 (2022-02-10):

VZ Eva Bltouch Dragon support?

sn0wfl4key, 2022-02-10:
There seems to be no support for the VZ Eva 2.4 for a bltouch, on the original it had some mounting holes in hte front face.
Is there something i have missed?

simonvez, 2023-01-04:
did you check the community mods ? im sure there are one

simonvez, 2023-03-28:
I highly suggest you upgrade to the Vz-Printhead. We dont develop arround Eva anymore

Closed 2023-03-28.

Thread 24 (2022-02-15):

Motor mounts inside the housing

ckvsoft, 2022-02-15:
Hi
I have a question about the x/y motors.
Have you ever had heat problems with the motors in the closed housing? It could be very warm inside.
Would it be better to place the motors outside?

lg Chris

mouamart, 2022-02-19:
I believe there is a printed part option to mount your motor outside the enclosure,

ckvsoft, 2022-02-21:
Yes there are. I wanted to know if there were heat problems with long prints when the motors are inside the housing. Or are LDO motors advisable here in any case?

Closed 2022-04-04.

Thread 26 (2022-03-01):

Missing Lm12uu mount stl file?

quocanhcgd, 2022-03-01:
In Bed assem, i can't find print part for LM12UU, but in Z up and down have it.
Is that missing or can't use Lm12uu?

simonvez, 2022-06-13:
thats what you need ? sorry for the long reply

Closed 2022-06-13.

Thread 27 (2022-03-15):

Link to cpap fan broken for USA

kdb424, 2022-03-15:
The aliexpress link to the fan is not working with the message "This item cannot be shipped to United States". Any chance there is an alternative link for a seller that ships to the US?

simonvez, 2022-06-07:
there are 2 links in the bom.. are both of them not working for US ?

simonvez, 2022-06-07:
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

the first link works : <html>
<body>
<!--StartFragment-->

https://s.click.aliexpress.com/e/_AEsHxz
--

<!--EndFragment-->
</body>
</html>

Closed 2022-06-07.

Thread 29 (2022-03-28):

FAN DUCT CAD WRONG

lipk888, 2022-03-28:
HI TEAM:
i just found issue about FAN duct, which show center hold not pass through.
can you help update CAD

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

simonvez, 2022-06-07:
sorry for the late reply. I have loaded the CAD for the Vz-Printhead. I downloaded the step file from github to be sure and loaded and it is corrected for me. Maybe you got the early release. But the cad is fine now. you can download it
thanks
Vez

Closed 2022-06-07.

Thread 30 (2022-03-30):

missing the fan base

psusong, 2022-03-30:
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
Hi, where can I find the printed drawings of this fan base

psusong, 2022-03-30:
i find https://www.thingiverse.com/thing:5252555

simonvez, 2022-06-07:
no.. only the small fan to save weight

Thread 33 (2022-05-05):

BOM no download link

waym99, 2022-05-05:
I can't download the BOM anymore. Need it for comparison and editing.

simonvez, 2022-05-05:
I Waym99.. not sure anything changed on our side. If you cant access the bom anymore, what error message you get? If you can access it and want to have a local copy, you could simply copy paste all the content to a local spreadsheet :)

waym99, 2022-05-05:
I can actually access it but not in the same way as the 235. It's somewhat restricted. I read some where you have to make it public.

Awesome project. Thank you for your effort!

simonvez, 2022-05-09:
please try now

drops77, 2022-05-09:
> please try now

Works now! Thank you

Closed 2022-06-07.

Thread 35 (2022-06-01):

Y-Gantry CAD and github page shows wrong pulley order

Arakon, 2022-06-01:
According to both the CAD and the [images here](https://github.com/VzBoT3D/VzBoT-Vz330/tree/master/Assemblies%20BOM%20and%20STL/Gantry/Y%20gantry/Printed%20Y%20Gantry), the pulleys are supposed to be one toothed, one smooth on each front and back.
However, the actual order to follow the belt orientation should be both toothed in front, both smooth in back.

simonvez, 2022-06-07:
Fixed the pictures

simonvez, 2022-06-08:
I need to stop sniffing glue apparently haha.. ok now its fixed

Closed 2022-06-07.

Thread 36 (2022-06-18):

Sherpa Mini mount bad geometry

Arakon, 2022-06-18:
The sherpa mini (misspelled "nini") STL [here](https://github.com/VzBoT3D/VzBoT-Vz330/blob/master/Assemblies%20BOM%20and%20STL/PrintHeads/EVA-Vz/STLs/Top-MGN9-Sherpa%20nini.stl) has a bulge in four areas that is blocking the internal hole where a long bolt has to pass through.
This can be fixed by drilling, but it doesn't seem like this is intentional.
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

simonvez, 2023-01-04:
thanks for reporting, and sorry for the late response. I don't have that cad unfortunately, but  will try to find who made it so we can fix it.

Closed 2023-02-20.

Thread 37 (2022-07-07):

I dont use social media and I have questions

dkuchay, 2022-07-07:
1.5 years into owning a Voron and I just noticed your project. I dont use social media so the concept of a custom 3d printer is challenging for me due to lack of an ability to ask a question. Can this printer do multiple materials or is the indirect drive going to limit to non TPU based filaments?

chrishenze, 2022-07-09:
Best place to ask question is on discord, there a lot of helpful people. A Vz is intended for very fast prints, but you can modifiy it as you wish. The print head uses direct drive with for example the lgx lite or the Vz-Hextrudort, so you can print most materials except hight temp engineering materials.

dkuchay, 2022-07-09:
Very much appreciate your reply. Thank you. I’ll continue to dive in to VzBot. Thankfully enough resellers carry parts for Voron I can stay abreast of things that users contribute. About the only drawback so far for me. There begins the breakage of the Voron experience though. Stock build sucks and a slight sour taste may result seeing how many mods it takes to get somewhat reliable. I’ve spent 5 years in industrial robotics and attracted to VzBot via gantry and simplicity. Discord more of a won’t for me. Too many bad actors there. Protecting our kids from it but having to use it for other reasons ourselves makes little sense. How cumbersome is the github discussion board? I see it as Vorons mistake for not using. Could have been great repo for mods and support for. Considering their engineers are also authors it again makes me think of a bad taste. IRC chat would even be better than discord for the automation. Lurk, record and filter. Find relevant information quickly. Discord for you is easy. For the user there is a rabbit hole factor where for one, I won’t use public chat for individualized support. Two I just don’t have the time to read each conversation that takes place upon the project in search of my needle within the haystack.  If I were in your shoes it would be an easy choice. I’ve spent 5 years assembling high speed assembly systems aka production lines,  that were sold to pharma. These included robotics, plc’s, vision systems and more. I may have viable ideas to contribute.  Wouldn’t you appreciate a report upon who else wouldn’t even take the time to contact you because they don’t agree with the support venue? Discord may repel those with greater levels of real world experience from going as far as I did as there is no way to ask a question to your project.

If the discussion board is not to your liking then fire it back at github and feel free to include this message. Microsoft owns them now and they are doing their own dev upon. Demand a better feature. They owe the community for all they did during the 80’s. Watch Netscape docu if you’re too young to remember. Discord is a no go as is FB as is twitter. I know it is for me and i just don’t know how many others I speak for. Do you?

Sent from my iPhone

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

Armoth1, 2022-07-19:
Totally agree with [dkuchay]. I real pity we cant get support on a non-public platform. There is a minority that makes this real unpleasant.

Runningtarrens, 2022-09-03:
The primary community spots are facebook and discord. I use discord. Its a very nice platform, the vzbot server is very nice and full of good people. Over 4k user and fighting at all. I dont understand what you mean, when you talk about non public platform, is this here a non public platform? why are you okay writing here but not on discord? discord is widely used not only for 3d Printer builder but also for vendors, its the best way to get in contact with them. so team would really hamper themselfs without the platform.

anyway, if you do not want to use Facebook or discord is fine, but the difficulty of the build is gona be a bit higher because you might need to figure things out on your own term. But as options there is the git with all neseccary parts uploaded, a complet CAD file. Which you can explore, disassemble and manipulate to your liking, even the usermods that where created and shared on Discord get uploaded into the Usermod repo here on git. There is a manual for the assembly of the printers and the most important settings. Building on top of this there are a lot of videos online on youtube, that shows part of the build, upgrades,configurations, tests and capabilities.

Documentation could alway be better, but please dont forget that its a young project and its only a handful of devs that work on the project. its no where near the size of the voron project/community. So if you still have questions and you feel like you have explored all your options, open an issue with a question here, it might take some time, but people will help.

Armoth1, 2022-09-06:
Hey,

Thank you for your reply. My account got hacked and some bad things
happened from there(FB) so since then I’m very wary. So I stay away and use
email to communicate mostly.

Please note I’m not trying to be difficult or in anyway negative about
VZbot and/or the community, quite the contrary.

Best,

On Sat, 3 Sep 2022 at 12:06, Runningtarrens ***@***.***>
wrote:

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

ganzgustav22, 2022-10-28:
This is something I find strange about the VzBot (and other 3dprinter projects). Why is there no forum somewhere? I've had a few hobbies the past years, so far every hobby had one or more forums where people would post their builds, questions, discussions etc. etc.

Now with 3D printers, there are some forums but they seem to be either deserted or populated mostly by peoply who print with 50mm/s and don't want to print faster.

Discord is just a chat, not really suitable for buidlogs and more complex discussions. Where are these things happening?

dkuchay, 2022-10-28:
I posed this question to GitHub wondering the exact same thing and it turns out every GitHub project can elect to activate a discussion board. GitHub suggested that I ask the project lead to activate this or to contact GitHub for help if they didn’t know how to do this. In stead this project along with other 3d printer projects knowingly omit the github in-project offered discussion board. Based on responses this won’t change. Since realizing this I’ve lost interest and have assumed developers to be incapable Sent from my iPhoneOn Oct 28, 2022, at 5:44 AM, ganzgustav22 ***@***.***> wrote:
This is something I find strange about the VzBot (and other 3dprinter projects). Why is there no forum somewhere? I've had a few hobbies the past years, so far every hobby had one or more forums where people would post their builds, questions, discussions etc. etc.
Now with 3D printers, there are some forums but they seem to be either deserted or populated mostly by peoply who print with 50mm/s and don't want to print faster.
Discord is just a chat, not really suitable for buidlogs and more complex discussions. Where are these things happening?

—Reply to this email directly, view it on GitHub, or unsubscribe.You are receiving this because you authored the thread.Message ID: ***@***.***>

simonvez, 2023-01-04:
Discord is way more than just a chat platform. It has FORUM type of posting now and much more. I dont have time and energy to support a Forum too. Discord , FB, Youtube, Instagram is already taking too much of my time :) Discord is probably the best plate for all your need. And like I said, it has evolved a lot with nice addons that you dont need a forum anymore

simonvez, 2023-01-04:
oh.. and we have build logs forum now ;)

Closed 2023-01-09.

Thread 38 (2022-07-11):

Hextrudort high motor mount feed gear problems

FloxRoxX, 2022-07-11:
Hi, i printed the HextrudOrt with the high motor mount (not the helical version). Additionally i use the original Bondtech gears and noticed, that the gears do not make good contact with the filament.

Hextrudort was printed on ABS like resin for high temp resistances on my elegoo mars. So accuracy cannot be the problem ;)

See picture, you can clearly see that the filament is only touching the left screw barely. Also with tensioning the gears fully up the tension isnt enought... Any help is appreaciated :)

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

EDIT:
Here a little video that shows the problem in action...

https://photos.app.goo.gl/UMnWPYBEVg9GL4wj9

simonvez, 2023-01-04:
there was a new model published that has an extra bolt at the bottom to help. But looking at your video it looks like the printed parts are not stiff enough maybe? Try with the new model it should help a lot

Closed 2023-01-09.

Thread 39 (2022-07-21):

No motor

Armoth1, 2022-07-21:

Armoth1, 2022-07-21:
Hi guys, just a fyi - re no motor mounts listed on BOM. Would be nice to add and show quantity needed and variants if applicable based on different build options

Runningtarrens, 2022-09-01:
motor mounts are printed. In the BOM is no list for the printed parts, its intended for the parts you need to buy.

Armoth1, 2022-09-03:
Got it thanks. What I'm looking for though is a place where you can see every part of the printer in one clean list like the BOM sheet. So that I cann easily tick off what I have (printed parts and BOM parts) as I'm finding it hard to keep track..  Perhaps not a problem, for most. Just thought I'd share it anyway. Thx for responding its much appreciated.  I'll look up the parts and put together a list for myself by combining BOM list with printed part names, not intending to make more work for you guys. Thx!

Runningtarrens, 2022-09-03:
you could make a copy of the BOM for all the parts that are not printed and then copy the lists of printed parts out of the manual. its not one big list but a handful of smaller, categorized in groups. maybe that would help you getting all the needed parts in one list.

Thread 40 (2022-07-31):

Source (f3d/step) files missing for dual motor mount

tonyshackelton, 2022-07-31:
Hi, I am trying to combine parts from the 535 rod mounts and dual motor mounts into a singular part for those that wish to modify the tronxy bed for VZBot use/enclosure. I am unable to locate the cad files, and have reached out via discord. I wanted to make an issue here, in case an admin does have these files, or if not, they could be merged into the repo once procured.

simonvez, 2023-01-04:
cad file can be found here: https://github.com/VzBoT3D/VzBoT-Vz330/tree/master/CAD/Z%20assembly/Dual%20Z%20motor%20mount

Closed 2023-01-04.

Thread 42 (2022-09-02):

Front Door Hinge Part 2 has 4.2mm holes to mount panel, but panel has 3.2mm holes

Arakon, 2022-09-02:
BOM specifies 4mm bolts, too.
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

I helped it using thin nylon washers, which just so happened to have the size of an M4 screw head.

Please either adjust the hole diameter in the enclosure step files or STL, and adjust the BOM.

Also, the build manual specifies M4x40 bolts to connect the two hinge halves, but that's too short, M4x50 is required at least.

simonvez, 2023-01-04:
Hi there, thanks for reporting this. sorry for the late reply. The front door holes were corrected a while ago. Its using M4 so the holes were changed to 4.3mm. Thanks

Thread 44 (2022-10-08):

Aluminum Y gantry stl files

vanatd, 2022-10-08:
Hello there!
First of all, thank you for your hard work! it looks amazing!

I was looking through the GitHub repo and did not find the STL file for the aluminum y gantry. Idk maybe you did not push it on purpose, but it would be very cool to have it.

Thank you in advance!

vanatd, 2022-10-09:
Seems like there are no stl files for the main parts in aluminum at all :(
Is there a way to use printed stl files for the CNC machine?

vanatd, 2022-10-11:
Thanks a lot for your response!
Unfortunately I can't buy it in Ukraine so far.
Anyway, you did a very cool and hard job, thanks a lot for doing that!
once I can buy these parts I definitely will do it!

Closed 2022-10-14.

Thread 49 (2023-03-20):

AWD trouble at slow speed

trackhacs, 2023-03-20:
I have AWD configuration with TMC5160. It works beautiful for normal printing, without any problems.

However, at (very) low speeds  and low acceleration, e.g. during klipper tuning_tower test with suggested acceleration of only 500,  one of the TMC is reporting "no load" and klipper chickens out.

Guess this is due to both motor pulling in same direction and that might cause one motor to see no load.

any experience with this?

simonvez, 2023-03-28:
I have personally never heard of that. Did you do the sync procedure ?

trackhacs, 2023-03-31:
yes - but I did only loose one motor per belt. just saw your (?) video about it and will try to loosen all 4 motors.

simonvez, 2023-04-01:
I do only 1 motor per belt too..but doing all 4 is better...just way harder

Closed 2023-08-04.

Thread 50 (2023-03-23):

Swapped file names

porkcube, 2023-03-23:
Looks like [exhaust middle cover 10mm Hepa filter.stl](https://github.com/VzBoT3D/VzBoT-Vz330/blob/master/Assemblies%20BOM%20and%20STL/enclosure/Exhaust%20filter%20-%20Fume%20extractor/Exhaust%20filter%20housing/STLs/exh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) and [exhaust middle cover 15mm Hepa filter.stl](https://github.com/VzBoT3D/VzBoT-Vz330/blob/master/Assemblies%20BOM%20and%20STL/enclosure/Exhaust%20filter%20-%20Fume%20extractor/Exhaust%20filter%20housing/STLs/exh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) files are swapped (e.g. 10mm is actually the 15mm / 15mm is actually the 10mm).

simonvez, 2023-03-24:
I think they are ok. the thicker 15mm filter will require a thinner stl part.

porkcube, 2023-03-31:
OH I see now, I misunderstood the `10mm` / `15mm` are for the filter's size and I was just comparing the models themselves - they're correct as is.

Closed 2023-03-28.

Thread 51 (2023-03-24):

Different knob-cab for NEMA17 Left and Right Motor mount with Tensioner

EmanueleGiannuzzi, 2023-03-24:
These 2 STL contain different models:
LEFT MOTOR MOUNT: https://github.com/VzBoT3D/VzBoT-Vz330/blob/master/Assemblies%20BOM%20and%20STL/Gantry/Motor%20Mounts/Printed/Left%20Motor%20Mount%20Nema17%20with%20Tensioner/STLs/k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
RIGHT MOTOR MOUNT: https://github.com/VzBoT3D/VzBoT-Vz330/blob/master/Assemblies%20BOM%20and%20STL/Gantry/Motor%20Mounts/Printed/Right%20Motor%20Mount%20Nema17%20with%20Tensioner/STLs/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

https://i.imgur.com/r04ShFW.png

They are 7mm and 9mm long.
Looking at the CAD, the correct one should be the one in the Right Motor mount folder (7mm).

simonvez, 2023-03-28:
Good catch ! thanks. I have updated it

Closed 2023-03-28.

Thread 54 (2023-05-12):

Printed Y gantry bottom has thin layer in nut hole

utubosk8er, 2023-05-12:
Haven't printed this part yet (Y_gantry_bottom_left.stl), but I do believe the center of a hole that nut sits should be a thru hole, otherwise it would block the tip of M5x30mm bolt from going through.
Is this something that needs to be drilled out or is this how its supposed to be?

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

jaarenhoevel, 2023-05-21:
I suppose that is on purpose to make it easier to print. That way the following round perimeters are not floating in the air.
You may want to print it with the flat side touching the build plate tho.

simonvez, 2023-08-04:
Yes its to avoid printing support. Need to punch through or drill through

Closed 2023-08-04.

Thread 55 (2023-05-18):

full printer step opening problem

Moreno-sky, 2023-05-18:
i have a problem during the opening of the step file of the full printer, my CAD software crash near the end of the opening

magnificu, 2023-07-03:
I have the same problem.

simonvez, 2023-08-04:
What software do you guys use?

simonvez, 2023-09-17:
You can try the web version instead. The full cad is huge and you need quite a good pc to load it

HumbleDeer, 2023-09-22:
One solution we can issue, is a CAD model with all step files placed in there separately.

Even better would be SLDPRT exports, as STEP files need to be "converted" from solid body definitions to solid bodies and given surfaces that are calculated at opening, before they're displayed.

EduardoMDSousa, 2023-09-22:
Wy? My old laptop with intel grafics 4gb ran Open The full CAD on Fusion360.

Closed 2023-09-17.

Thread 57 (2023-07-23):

Octopus Board

DeForestDiamond, 2023-07-23:
Hey!

In the BOM one if the options is the BTT Octopus but I can't find a config or bin file for it anywhere. Would you happen to have one kicking around? Preferably the config as I bought the "Max EZ" version and will probably have to change pins.

I did try making one but I have nearly zero experience and I'm too afraid to try it lol.

Thanks!!!

simonvez, 2023-08-04:
Im sure there are people that run this board. Might want to in discord or fb

Closed 2023-08-04.

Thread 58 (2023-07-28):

Boot Video Update for Raspbian

recrudesce, 2023-07-28:
Latest Raspbian version doesn't include a VLC player with mmal support, therefore your boot video details don't work.

However, you can easily make it work as follows

`sudo apt install mplayer`

Then rather than using cvlc in the `splash.service`, you instead use this

`ExecStart=/bin/bash -c "mplayer -nosound -nolirc -vf scale=800:480 -vo fbdev2:/dev/fb0 /home/pi//intro1.mp4" &`

Everything else stays the same.

18Markus1984, 2023-08-29:
I now tried omxplayer, cvlc and mplayer nothing worked :(  Why are there the two // instead of  /home/pi/bootvideo?

recrudesce, 2023-08-29:
Typo, but it's irrelevant.

Check your device (fbdev2 etc) and check that the mp4 is in the path you're referencing.

18Markus1984, 2023-08-29:
I tryed to run it, but KlipperScreen doesn't allow it I think.

pi@peter:~ $ mplayer -vo fbdev2 -fs /home/pi/bootvideo/peter.mp4
MPlayer 1.4 (Debian), built with gcc-10 (C) 2000-2019 MPlayer Team
do_connect: could not connect to socket
connect: No such file or directory
Failed to open LIRC support. You will not be able to use your remote control.

Playing /home/pi/bootvideo/peter.mp4.
libavformat version 58.45.100 (external)
libavformat file format detected.
[mov,mp4,m4a,3gp,3g2,mj2 @ 0x766cfc90]Protocol name not provided, cannot determine if input is local or a network protocol, buffers and access patterns cannot be configured optimally without knowing the protocol
[lavf] stream 0: video (h264), -vid 0
VIDEO:  [H264]  800x480  24bpp  30.000 fps   82.8 kbps (10.1 kbyte/s)
==========================================================================
Opening video decoder: [ffmpeg] FFmpeg's libavcodec codec family
libavcodec version 58.91.100 (external)
Selected video codec: [ffh264] vfm: ffmpeg (FFmpeg H.264)
==========================================================================
Clip info:
 major_brand: isom
 minor_version: 512
 compatible_brands: isomiso2avc1mp41
 encoder: Lavf58.76.100
Load subtitles in /home/pi/bootvideo/
Audio: no sound
Starting playback...
Could not find matching colorspace - retrying with -vf scale...
Opening video filter: [scale]
[fbdev2] Can't put VSCREENINFO: Invalid argument
[fbdev2] Can't put VSCREENINFO: Invalid argument
Movie-Aspect is undefined - no prescaling applied.
[fbdev2] Can't put VSCREENINFO: Invalid argument
[fbdev2] Can't put VSCREENINFO: Invalid argument
[swscaler @ 0x767823e8]bicubic scaler, from yuv420p to rgb565le using C
[swscaler @ 0x767823e8]No accelerated colorspace conversion found from yuv420p to rgb565le.
[swscaler @ 0x767823e8]using unscaled yuv420p -> rgb565le special converter
VO: [fbdev2] 800x480 => 800x480 BGR 16-bit  [fs]
V:  16.5   0/  0 16% 32%  0.0% 0 0

Exiting... (End of file)

18Markus1984, 2023-08-29:
I deleted KlipperScreen because I didn't find an easy way to close it, and Kiauh makes it easy to reinstall. I got the video playing but only when KlipperScreen is deleted, and I have some weird artifacts.

```
pi@peter:~ $ mplayer -vo fbdev2 -fs /home/pi/bootvideo/peter.mp4
MPlayer 1.4 (Debian), built with gcc-10 (C) 2000-2019 MPlayer Team
do_connect: could not connect to socket
connect: No such file or directory
Failed to open LIRC support. You will not be able to use your remote control.

Playing /home/pi/bootvideo/peter.mp4.
libavformat version 58.45.100 (external)
libavformat file format detected.
[mov,mp4,m4a,3gp,3g2,mj2 @ 0x76724c90]Protocol name not provided, cannot determi                                                                                                                                                             ne if input is local or a network protocol, buffers and access patterns cannot b                                                                                                                                                             e configured optimally without knowing the protocol
[lavf] stream 0: video (h264), -vid 0
VIDEO:  [H264]  800x480  24bpp  30.000 fps   82.8 kbps (10.1 kbyte/s)
==========================================================================
Opening video decoder: [ffmpeg] FFmpeg's libavcodec codec family
libavcodec version 58.91.100 (external)
Selected video codec: [ffh264] vfm: ffmpeg (FFmpeg H.264)
==========================================================================
Clip info:
 major_brand: isom
 minor_version: 512
 compatible_brands: isomiso2avc1mp41
 encoder: Lavf58.76.100
Load subtitles in /home/pi/bootvideo/
Audio: no sound
Starting playback...
Could not find matching colorspace - retrying with -vf scale...
Opening video filter: [scale]
[fbdev2] Can't put VSCREENINFO: Invalid argument
[fbdev2] Can't put VSCREENINFO: Invalid argument
Movie-Aspect is undefined - no prescaling applied.
[fbdev2] Can't put VSCREENINFO: Invalid argument
[fbdev2] Can't put VSCREENINFO: Invalid argument
[swscaler @ 0x767d73e8]bicubic scaler, from yuv420p to rgb565le using C
[swscaler @ 0x767d73e8]No accelerated colorspace conversion found from yuv420p t                                                                                                                                                             o rgb565le.
[swscaler @ 0x767d73e8]using unscaled yuv420p -> rgb565le special converter
VO: [fbdev2] 800x480 => 800x480 BGR 16-bit  [fs]
V:  16.5   0/  0 20% 32%  0.0% 0 0

Exiting... (End of file)
```

https://github.com/VzBoT3D/VzBoT-Vz330/assets/52409213/cb10a43f-9033-43ff-a7d2-dec8673c063d

stonemandave, 2023-10-01:
I got the first intro video to work but the second doesn't. Do you know how i can convert to mplayer.

su - pi -c "sleep 2 | DISPLAY=:0 /usr/bin/cvlc -f --quiet --no-video-title --play-and-exit --mmal-display DSI-1 /home/pi/bootvideo/intro2.mp4"

HumbleDeer, 2023-10-02:
mplayer is software, not a format or codec.

o1hitman1o, 2024-01-15:
VLC works for me. Just need to apt install vlc

/etc/systemd/system/splash.service
*********
[Unit]
Description=Splash screen
DefaultDependencies=no
After=local-fs.target

[Service]
User=pi
ExecStart=nohup /bin/bash -c "DISPLAY=:0 /usr/bin/cvlc -f --quiet --no-video-title --play-and-exit --mmal-display DSI-1 /home/pi/boot_video/boot.mp4" &
StandardInput=tty
StandardOutput=tty

[Install]
WantedBy=sysinit.target

*********
I then add the second video to cover more of the booting time.
/etc/rc.local
Add this
su - pi -c "sleep 2 | DISPLAY=:0 /usr/bin/cvlc -f --quiet --no-video-title --play-and-exit --mmal-display DSI-1 /home/pi/boot_video/boot2.mp4" &

Before the exit 0

Save and reboot

HumbleDeer, 2024-01-17:
It's come to my attention a while back that there's a good chunk of people still running on Debian Buster. Those will have wildly different issues from subsequent versions, especially against the latest.

An example: A compatibility package present in Debian 11 was removed in Debian 12. This is causing issues with python library access and what libraries to use in regards to resonance measurements.

The issues coming forth from this are still undocumented as of now.

Could you all please list your specific distribution, version, and version numbers? Use `uname -a` to get all the identifying information.

o1hitman1o, 2024-01-17:
Linux mainsailos 6.1.21-v8+ #1642 SMP PREEMPT Mon Apr  3 17:24:16 BST 2023 aarch64 GNU/Linux

Treintjes, 2024-01-25:
thank you! this was the only way to git working on 64 bit mainsail installation! worked perfectly

Closed 2025-01-02.

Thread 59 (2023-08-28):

Add fan cover STL to Mellow STL list

1980alexGS, 2023-08-28:
Just an easy one - please add Assemblies BOM and STL/electronics/Back Electronic bay/Fly Super8/FlySuper8 fan cover.stl  - it's not in the Mellow STLs :)

Thanks

pbsuper, 2023-08-29:
issue solved.

Closed 2023-08-29.

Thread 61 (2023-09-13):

printer.cfg replacement in the docs?

1980alexGS, 2023-09-13:
Hello - can the file here on Github named 330AWD-printer.cfg replace the printer.cfg linked at https://docs.vzbot.org/vz330_mellow/electronics/Printer_Config - the link there seems to be broken? Thanks

EduardoMDSousa, 2023-09-13:
Yes 330awd is the printer.cfg just rename it

1980alexGS, 2023-09-15:
Thanks Eduardo - link at https://docs.vzbot.org/assets%5Cimages%5Cmanual%5Cvz330_mellow%5Celectronics%5CPrinter_config%5Cprinter.cfg still broken

EduardoMDSousa, 2023-09-15:
Yes i see , the page admin need to Change the file name, becase was Changed. 👍

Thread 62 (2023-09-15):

Mellow 330 STL list suggested changes

1980alexGS, 2023-09-15:
1. I think the items in https://github.com/VzBoT3D/VzBoT-Vz330/tree/master/Assemblies%20BOM%20and%20STL/enclosure/Front%20door%20latches/Magnetic%20latch
should replace the different door latch items in 'Mellow kit - all STLs' - Enclosure/Locking latch, since the kit now includes magnets.

2. The Back Electronic Bay section contains 'Front cover', 'Back cover', and 'screen mount frame' which I don't think belong there, because they appear in the Screen Mount section - please consider removing them from Back Electronic Bay.

3. Enclosure/Panel Trim - 'Trim - center x14' should be x16. Four in each side panel and eight in the top hat.

4. Vz-Printhead - 'Fan duct 2510-With flange for Vz-Printhead' - is it possible to increase hole sizes to 2.5mm, since the kit includes 4x M3x14mm screws which work for mounting the fan as long as the holes are drilled out to 2.5mm. I guess this is probably easier than changing the screws in the kit :)

5. - optionally - consider removing the 2020 Endcaps from the Frame section (they didn't fit for me and they seem unnecessary because the extrusion ends are coloured black), plus the Foot Spacer needs to be about 3.6mm thick to suit the rubber feet supplied in the kit (perhaps indicate this in the name of the file if it is difficult to change the size of the STL)

Thanks!

EduardoMDSousa, 2023-09-15:
Hi the stl are genéric, for all options , kit, and self sorced frame etc , still the best , is download the full printer CAD, and export , since vez keep all parts updated 1st on cad .

1980alexGS, 2023-09-15:
Ok, but I believe the Mellow 330 STL list.zip file should contain the STLs relevant to the Mellow 330 kit - and that specifically is what I’m trying to help with here.

I understand that STLs in other places can remain generic, i.e. both types of latches, different hole sizes, different display housings etc.

Thanks

simonvez, 2023-09-15:
all done

Closed 2023-09-15.

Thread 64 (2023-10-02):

HDMI cutouts for mellow fly LCD would've been nice

yuriy-yarosh, 2023-10-02:
There's a HDMI + jack cutout missing in the mellow LCD [back  cover](https://github.com/VzBoT3D/VzBoT-Vz330/blob/master/Assemblies%20BOM%20and%20STL/electronics/Screen%20Mount/Mellow-Fly%20Version/Back%20cover.stl) mount STL.
Front panel needs a bit of a wider cutout as well.
Maybe worth making a separate HDMI version ?

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

HumbleDeer, 2023-10-02:
Is this a different display board from the one the case was made for?

yuriy-yarosh, 2023-10-02:
@HumbleDeer No, it's just the display board has multiple adapters for various interfaces.
Mellow vzbot kits are shipped with a DSI adapter for rPI, but DSI is somewhat rPI exclusive, so it make sense to replace it with a HDMI+USB to FRC adapter (flex ribbon) instead.

Closed 2025-01-02.

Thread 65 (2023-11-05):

Corrupted DXF files of panels

montyx99, 2023-11-05:
I've tried to open in multiple viewers the Back electronic panel.dxf and the Bottom panel.dxf files and I get the following error from all of the viewers:
Error: Unexpected end of input: EOF group not read before end of file. Ended on code.

Please review! Thanks in advance

HumbleDeer, 2023-11-19:
I can now confirm this is indeed the case.

Some files are returning errors in Inkscape and LibreOffice Draw, but not in Fusion360. This is probably due to some file export incompatibility or error.

I will be investigating the cause.

HumbleDeer, 2023-11-19:
FreeCAD has no issues importing the lines in the drawing, but when it does import, it throws all line sections into a base object. The one "Sketch" F360 sees on the original is now a couple dozen different bits and pieces. I wonder if this has any relation to this issue.

I can't re-export as DXF due to not having the license for it

HumbleDeer, 2023-11-19:
The Fusion360 loaded file shows the following lump (img1) on the right side holes, which Solid Edge does too (img2). Solid Edge opens the file just fine though.
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

In addition to this, it looks like all lines in the drawings are double-exported due to automatic projection of the parts into the sketch plane.

Closed 2025-01-02.

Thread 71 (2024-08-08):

Link in Cad/Printheads is incorrect

Wojimus, 2024-08-08:
Tiny thing, both links in Cad/Printheads/readme.md link to the CNC version. The link for the printed version:
> If you are looking for the Printed version: https://github.com/VzBoT3D/Vz-Printhead

redirects to the cnc version. I believe the correct link should be https://github.com/VzBoT3D/Vz-Printhead-Printed

pbsuper, 2025-01-02:
Thanks for letting us know. The link has been fixed now.

Closed 2025-01-02.

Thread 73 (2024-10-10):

BOM List VZ330 error

kompumaster, 2024-10-10:
Small error in list:

Fasteners: T Nut **M3** - T Nut **M4**

kompumaster, 2024-10-10:
330x330mm, Double Sided PEI Spring Steel Sheet + Magnetic Base - broken link

pbsuper, 2025-01-04:
issue corrected.

Closed 2025-01-04.

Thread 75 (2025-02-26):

Web CAD

fil0512, 2025-02-26:
The hyperlink of the Autodesk Web CAD is not working.

pbsuper, 2025-05-15:
links fixed.

Closed 2025-05-15.

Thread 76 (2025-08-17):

Bearing Mounts

wilsongis, 2025-08-17:
On page 12 of the printer parts manual, it mentions I need to print 4x "Bearing Mounts". I have looked at all the STLs, and none have "Bearing Mount" in the name. What STL am I looking for?

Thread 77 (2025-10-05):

KlipperScreen theme/SplashScreen

Bersaker, 2025-10-05:
Hello,
I was just about to set up the splash screen, but unfortunately it doesn't work anymore because Bookworm doesn't have /etc/rc.local.
Is there another solution?

andersevenrud, 2025-10-05:
You could try the way I set it up om ny machine: https://gist.github.com/andersevenrud/957100c66fc2a746f6cb5fa2b0ba8aba

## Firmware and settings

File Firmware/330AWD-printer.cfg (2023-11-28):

### For Fly Super 8 V1.3 ####
### And Mellow Kit  ####
### For Fly Super pro 8, the SPI bus is spi1A
### For Fly Super 8 V1.3, the SPI bus is spi3

[include mainsail.cfg]
[include timelapse.cfg]
[include Exclude_Object.cfg]
[include Start_Stop.cfg]
[include Macro.cfg]
[include Speed.cfg]
[display_status]
[exclude_object]
[virtual_sdcard]
path: ~/gcode_files
[pause_resume]
recover_velocity: 350

# Enable arcs support for Orcaslicer.
[gcode_arcs]
resolution: 0.1

##### VzBoT############
#######################

[printer]
kinematics: corexy
max_velocity: 2500
max_accel: 10000
#max_accel_to_decel: 5000
max_z_velocity: 20
max_z_accel: 1500
square_corner_velocity: 10

########################
########################


[mcu]
serial: /dev/serial/by-id/usb-Klipper_stm32f407xx_3E0023000E47323236333832-if00  # put your own Serial here.
#restart_method: command

[temperature_sensor FLY-Super8]
sensor_type: temperature_mcu

[mcu rpi]
serial: /tmp/klipper_host_mcu

[temperature_sensor raspberry_pi]
sensor_type: temperature_host
min_temp: 10
max_temp: 100

########################
########################

[stepper_x]
##	in M6 position
step_pin: PE0
dir_pin: PG3
enable_pin: !PG4
rotation_distance: 40
microsteps: 16
full_steps_per_rotation: 200  
endstop_pin: PF10            #make sure to set the correct pin here.
position_endstop: 0
position_min: 0
position_max: 330
homing_speed: 50 
homing_retract_dist: 0

[tmc5160 stepper_x] 
#spi_bus: spi3
cs_pin: PG2
#diag_pin: PA8
interpolate: false
run_current: 1.9
sense_resistor: 0.033
spi_software_mosi_pin: PB5
spi_software_miso_pin: PB4
spi_software_sclk_pin: PB3
#driver_SGT: -64 # -64 is most sensitive value, 63 is least sensitive
driver_TBL: 1
driver_TOFF: 3
driver_DISS2G: 1
driver_DISS2VS: 1


[stepper_x1]
##	in M5 position
step_pin: PE1
dir_pin: !PF0
enable_pin: !PC15
rotation_distance: 40
microsteps: 16
full_steps_per_rotation: 200
#endstop_pin: tmc5160_stepper_x:virtual_endstop 

[tmc5160 stepper_x1] 
#spi_bus: spi3
cs_pin: PF1
#diag_pin: PD6
interpolate: false
run_current: 1.9
sense_resistor: 0.033
spi_software_mosi_pin: PB5
spi_software_miso_pin: PB4
spi_software_sclk_pin: PB3
#driver_SGT: -64 # -64 is most sensitive value, 63 is least sensitive
driver_TBL: 1
driver_TOFF: 3
driver_DISS2G: 1
driver_DISS2VS: 1


[stepper_y]
##	in M4 position
step_pin: PE15
dir_pin: !PE11
enable_pin: !PF2
rotation_distance: 40
microsteps: 16
full_steps_per_rotation: 200  
endstop_pin: PC0                 #make sure to set the correct pin here.
position_endstop: -0
position_min: 0
position_max: 330
homing_speed: 50  
homing_retract_dist: 0

[tmc5160 stepper_y] 
#spi_bus: spi3
cs_pin: PE10
#diag_pin: PD7
interpolate: false
run_current: 1.9
sense_resistor: 0.033
spi_software_mosi_pin: PB5
spi_software_miso_pin: PB4
spi_software_sclk_pin: PB3
#driver_SGT: -64 # -64 is most sensitive value, 63 is least sensitive
driver_TBL: 1
driver_TOFF: 3
driver_DISS2G: 1
driver_DISS2VS: 1

[stepper_y1]
##	in M3 position
step_pin: PE14
dir_pin: PE8
enable_pin: !PE9
rotation_distance: 40
microsteps: 16
full_steps_per_rotation: 200
#endstop_pin: tmc5160_stepper_y:virtual_endstop  

[tmc5160 stepper_y1] 
#spi_bus: spi3
cs_pin: PE7
#diag_pin: PG9
interpolate: false
run_current: 1.9
sense_resistor: 0.033
spi_software_mosi_pin: PB5
spi_software_miso_pin: PB4
spi_software_sclk_pin: PB3
#driver_SGT: -64 # -64 is most sensitive value, 63 is least sensitive
driver_TBL: 1
driver_TOFF: 3
driver_DISS2G: 1
driver_DISS2VS: 1

#########################

[stepper_z]
## In M1 position
step_pin: PE3
dir_pin: !PF13
enable_pin: !PF14
microsteps: 32
rotation_distance: 4
endstop_pin:               #make sure to set the correct pin here.
#position_endstop: 0.0
position_max: 400
full_steps_per_rotation: 200
homing_retract_dist: 5.0
homing_positive_dir: false
homing_speed: 5.0
second_homing_speed: 2.5
[tmc2209 stepper_z]
interpolate: false
uart_pin: PF12
run_current: 1.2
stealthchop_threshold: 0

[extruder]
## In M0 position
### Vz-HextrudORT
step_pin: PE2
dir_pin: PC5
enable_pin: !PF11
microsteps: 16
#Alu VZhextrudort Moons 8T
rotation_distance: 22.2
Gear_ratio: 50:8
#Alu VZhextrudort Moons 10T
#rotation_distance: 22 
#gear_ratio: 50:10 
#VZHextrudort LDO 20mm
#rotation_distance: 4.71
nozzle_diameter: 0.5
filament_diameter: 1.750

heater_pin: PB0
sensor_type: PT1000
sensor_pin: PF4

#control: pid
#pid_Kp=28.737 
#pid_Ki=1.935 
#pid_Kd=106.684
min_temp: 0
max_temp: 400
full_steps_per_rotation: 200
max_extrude_only_distance: 1000.0
max_extrude_cross_section: 500
max_extrude_only_velocity: 200
max_extrude_only_accel: 10000
min_extrude_temp: 0
pressure_advance: 0.02
pressure_advance_smooth_time: 0.03

[tmc2209 extruder]
uart_pin: PC4
interpolate: false
run_current: 0.7
sense_resistor: 0.110

########################
########################

[heater_bed]
heater_pin: PE5
sensor_type: Generic 3950
sensor_pin: PC1
#control: pid
#pid_Kp: 66.746
#pid_Ki: 3.504
#pid_Kd: 317.878
min_temp: 0
max_temp: 130


########################
#### FANS ##############
########################

[fan]
##	Print Cooling Fan - PF8
pin: PF8
max_power: 1
cycle_time: 0.002
hardware_pwm: false
shutdown_speed: 0

[heater_fan hotend_fan]
##	Hotend Fan - FAN0 Connector
## in case of a watercooler that is 24V use a Heater Pin like PF7 Heat3 for a larger mosfet that can handle more amps.
pin: PA0
max_power: 1.0
kick_start_time: 0.5
heater: extruder
heater_temp: 50.0

#[fan_generic Exhaust_fan]
##  exhaust fan - In FAN4
#pin: PA15
#max_power: 1
#shutdown_speed: 0
#kick_start_time: 0.1
#off_below: 0.10

#[fan_generic chamber_fan]
###  chamber fan - In FAN9 Positon
#pin: PD15
#max_power: 1
#shutdown_speed: 0
#kick_start_time: 0.1
#off_below: 0.10

#[fan_generic RSCS]
##  RSCS Fans - In FAN1 Positon
#pin: PA1
#max_power: 1
#shutdown_speed: 0
#kick_start_time: 0.1
#off_below: 0.10

#[controller_fan driver_fan] 
# This is if you connect your driver fan to Super8 
#or if you want to add fan to the Super8. Other wise connect them in the driver fan ports
#stepper: stepper_x
#pin: PD14
#max_power: 1
#shutdown_speed: 0
#kick_start_time: 0.1
#off_below: 0.10

########################
########################

#[temperature_sensor chamber]  optional for chamber temp
#sensor_type: NTC 100K MGB18-104F39050L32
#pullup_resistor: 4700
#sensor_pin: PF5
#min_temp: 0
#max_temp: 60
#gcode_id: C: C

#[temperature_sensor Bed_Edge]
#Sensor_type: Generic 3950
#sensor_pin:PF4

###########################################
#########Custom PINs Definition ############
###########################################

#[output_pin LED]
#In FAN8 position if 12 or 5V
#When 24V use a heater pin like Heat4 PF6
#pin: PF6
#pwm: false
#value: 1
#shutdown_value:1
### gcode command: SET_PIN PIN=LED value=0 to 1

[idle_timeout]
timeout: 1800
gcode =
  {% if printer.pause_resume.is_paused %}
    M104 S0
  {% else %}
    TURN_OFF_HEATERS
    #M84
  {% endif %}

################################################################################################
##                                        Probe                                               ##
################################################################################################

#[bed_screws]
#screw1: 20,20
#screw2: 20,290
#screw3: 290,290
#screw4: 290,20

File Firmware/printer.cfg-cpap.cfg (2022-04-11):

[include mainsail.cfg]
[include timelapse.cfg]

##### VzBoT############
#######################

[printer]
kinematics: corexy
max_velocity: 2500
max_accel: 10000
max_accel_to_decel: 10000
max_z_velocity: 20
max_z_accel: 1000
square_corner_velocity: 10

########################
########################


[mcu]
serial:/dev/serial/by-id/usb-Klipper_stm32f407xx_580040000250304235323120-if00
#restart_method: command

[mcu rpi]
serial: /tmp/klipper_host_mcu

[adxl345]
cs_pin: rpi:None

[resonance_tester]
accel_chip: adxl345
probe_points:
    155,155,20  # an example

########################
########################

[stepper_x]
step_pin: PE2  # Drive0
dir_pin: PC5
enable_pin: !PF11
microsteps: 16
rotation_distance: 40
endstop_pin: PG11
position_endstop: -16
position_min: -16
position_max: 315
homing_speed: 45
full_steps_per_rotation: 200
homing_retract_dist: 0
homing_positive_dir: false
step_pulse_duration: 0.000001
#step_pulse_duration: 0.000000100
#[tmc2209 stepper_x]
#uart_pin: PC4
#interpolate: true
#run_current: 1.7
#hold_current: 1
#sense_resistor: 0.110
#stealthchop_threshold: 0
[tmc5160 stepper_x]
interpolate: false
cs_pin: PC4
#diag1_pin: PG12
run_current: 1.8
#hold_current: 0.5
spi_bus: spi3
driver_SGT: 1
sense_resistor: 0.075




[stepper_y]
step_pin: PE3  # Drive1
dir_pin: PF13
enable_pin: !PF14
microsteps: 16
rotation_distance: 40
endstop_pin: ^PG12
position_endstop: -8
position_min: -8
position_max: 315
homing_speed: 45
full_steps_per_rotation: 200
homing_retract_dist: 0
homing_positive_dir: false
step_pulse_duration: 0.000001

#[tmc2209 stepper_y]
#uart_pin: PF12
#interpolate: true
#run_current: 1.7
#hold_current: 1
#sense_resistor: 0.110
#stealthchop_threshold: 0
[tmc5160 stepper_y]
interpolate: false
cs_pin: PF12
#diag1_pin: PG11
run_current: 1.8
#hold_current: 0.5
spi_bus: spi3
driver_SGT: 1
sense_resistor: 0.075



[stepper_z]
step_pin: PE15
dir_pin: !PE11
enable_pin: !PF2
microsteps: 16
rotation_distance: 4
endstop_pin: !PG10
position_endstop: 0.0
position_max: 400
full_steps_per_rotation: 200
homing_retract_dist: 5.0
homing_positive_dir: false
homing_speed: 5.0
second_homing_speed: 2.5
step_pulse_duration: 0.000004
[tmc2209 stepper_z]
interpolate: false
uart_pin: PE10
run_current: 1.4
hold_current: 1
sense_resistor: 0.110
stealthchop_threshold: 0

[extruder]
### Vz-HextrudORT
step_pin: PE14
dir_pin: !PE8
microsteps: 16
enable_pin: !PE9
#Vz-Hextrudort rotation_distance: 4.55  
rotation_distance: 4.637
nozzle_diameter: 0.5
filament_diameter: 1.750
heater_pin: PB0
sensor_type: PT1000
#sensor_type: ATC Semitec 104NT-4-R025H42G
sensor_pin: PF4
###
control: pid
pid_kp = 22.348
pid_ki = 1.655
pid_kd = 75.426
min_temp: 0
max_temp: 400
full_steps_per_rotation: 200
max_extrude_only_distance: 1000.0
max_extrude_cross_section: 500
max_extrude_only_velocity: 200
max_extrude_only_accel: 10000
min_extrude_temp: 0
pressure_advance: 0.075
pressure_advance_smooth_time: 0.04
step_pulse_duration: 0.000004
[tmc2209 extruder]
interpolate: false
uart_pin: PE7
run_current: 0.8
hold_current: 0.5
sense_resistor: 0.110
stealthchop_threshold: 0
#[tmc5160 stepper_y]
#interpolate: false
#cs_pin: PF15
#run_current: 0.7
#hold_current: 0.3
#spi_bus: spi3
#driver_SGT: 1
#sense_resistor: 0.075


########################
########################

[heater_bed]
heater_pin: PE5
sensor_type: Generic 3950
sensor_pin: PC1
control: pid
pid_Kp: 66.746
pid_Ki: 3.504
pid_Kd: 317.878
min_temp: 0
max_temp: 130


########################
#### FANS ##############
########################

[fan]
##	Print Cooling Fan - GPIO26
pin: rpi:gpio26
max_power: 1
cycle_time: 0.002
hardware_pwm: false
shutdown_speed: 0

[heater_fan hotend_fan]
##	Hotend Fan - FAN0 Connector
pin: PA0
max_power: 1.0
kick_start_time: 0.5
heater: extruder
heater_temp: 50.0

[fan_generic Exhaust_fan]
##  exhaust fan - In FAN4
pin: PA15
max_power: 1
shutdown_speed: 0
kick_start_time: 0.1
off_below: 0.10

[fan_generic chamber_fan]
##  chamber fan - In FAN9 Positon
pin: PD15
max_power: 1
shutdown_speed: 0
kick_start_time: 0.1
off_below: 0.10

[fan_generic RSCS]
##  RSCS Fans - In FAN1 Positon
pin: PA1
max_power: 1
shutdown_speed: 0
kick_start_time: 0.1
off_below: 0.10

[controller_fan driver_fan]
stepper: stepper_x
pin: PB11
max_power: 1
shutdown_speed: 0
kick_start_time: 0.1
off_below: 0.10

########################
########################

[temperature_sensor chamber]
sensor_type: Generic 3950
pullup_resistor: 4700
sensor_pin: PF9
min_temp: 0
max_temp: 60
gcode_id: C: C


[temperature_sensor raspberry_pi]
sensor_type: temperature_host
min_temp: 10
max_temp: 100



########################
########################

[pause_resume]
recover_velocity: 350

########################
########################

[filament_switch_sensor sentinel]
pause_on_runout: true
switch_pin: PA8
runout_gcode:
	G91
    G1 E-30 F2500
  	G90
	G1 X0 Y0 F30000
  	M104 S0

########################
########################

#[homing_override]
#set_position_z: 0
#axes: xy
#gcode:
# G0 Z3 F200
# G28 y0 
# G28 x0
# G28 Z0

########################
########################

[firmware_retraction]
retract_length: 0.3
retract_speed: 100
unretract_extra_length: 0
unretract_speed: 100

###########################################
#########Custom PINs Definition ############
###########################################



#[output_pin DSLR]
#pin: rpi:gpio26
#pwm: False
#value: 1
#shutdown_value:1

[output_pin LED]
#In FAN8 position
pin: PD14
pwm: false
value: 1
shutdown_value:1
### gcode command: SET_PIN PIN=LED value=0 to 1



################################################################################################
################################################################################################
#####				MACROS					

##################
[gcode_macro RETRACTION_UP]
gcode:
    {% set CRLEN = printer.firmware_retraction.retract_length|float %}
    {% set NRLEN = CRLEN|float + 0.1 %}
    { action_respond_info("current retract_length %.2f, new retract_length %.2f" % (CRLEN, NRLEN))  }
    SET_RETRACTION RETRACT_LENGTH={NRLEN}    

[gcode_macro RETRACTION_DOWN]
gcode:
    {% set CRLEN = printer.firmware_retraction.retract_length|float %}
    {% set NRLEN = CRLEN|float - 0.1 %}
    { action_respond_info("current retract_length %.2f, new retract_length %.2f" % (CRLEN, NRLEN))  }
    SET_RETRACTION RETRACT_LENGTH={NRLEN}   


#[gcode_macro SET_RETRACTIONLENGTH]
#gcode:
#  SET_RETRACTION RETRACT_LENGTH={params.LENGTH|float}
#  GET_RETRACTION

########################	
[gcode_macro exhaustfan_on]
gcode: 
	SET_FAN_SPEED FAN=Exhaust_fan SPEED=1
###	
	
[gcode_macro exhaustfan_off]
gcode: 
	SET_FAN_SPEED FAN=Exhaust_fan SPEED=0
	
	
###		
	
[gcode_macro enclosurefan_on]
gcode: 
	SET_FAN_SPEED FAN=chamber_fan SPEED=1

###			
	
[gcode_macro enclosurefan_off]
gcode: 
	SET_FAN_SPEED FAN=chamber_fan SPEED=0


[gcode_macro RSCS_on]
gcode: 
	SET_FAN_SPEED FAN=RSCS SPEED=1
###	
	

[gcode_macro RSCS_off]
gcode: 
	SET_FAN_SPEED FAN=RSCS SPEED=0
		
###

[gcode_macro LED_on]
gcode:
	SET_PIN PIN=LED value=1   


[gcode_macro LED_off]
gcode:
	SET_PIN PIN=LED value=0  

###	
	
[gcode_macro PA_tunning]
gcode: 
	SET_VELOCITY_LIMIT SQUARE_CORNER_VELOCITY=1 ACCEL=500
	TUNING_TOWER COMMAND=SET_PRESSURE_ADVANCE PARAMETER=ADVANCE START=0 FACTOR=.005


#####

[gcode_macro POWER_OFF]
gcode:
  {action_call_remote_method("set_device_power",
                             device="tplink",
                             state="off")}
#####	

[gcode_macro TEST_RESONNANCES_X]
gcode:
 TEST_RESONANCES AXIS=X


[gcode_macro TEST_RESONNANCES_Y]
gcode:
 TEST_RESONANCES AXIS=Y

[gcode_macro DUMP_WARNINGS]
description: Debug: Print all warning messages from klipper
gcode:
  {% set parameters = ["printer.configfile.warnings:"] %}
  {% for warning in printer.configfile.warnings %}
      {% set parameters = parameters.append("%s -> %s -> %s\n%s" % (warning.type, warning.section, warning.option, warning.message)) %}
  {% endfor %}
  {action_respond_info(parameters|join("\n"))}



################################################################################################
################################################################################################



[virtual_sdcard]
path: ~/gcode_files

########################
########################

[display_status]

########################
########################

[bed_screws]
screw1: 20,20
screw2: 20,290
screw3: 290,290
screw4: 290,20


########################
########################

[input_shaper]
shaper_freq_x: 96.2
shaper_type_x: ei
shaper_freq_y: 69
shaper_type_y: mzv

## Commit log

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2021-10-18 STLs for motor mounts
    [Left Motor Mount Nema17 BOTTOM.stl, Left Motor Mount Nema17 TOP.stl, Motor Mount Left Nema17.f3d]
2021-10-22 STLs added for Fram
    new Frame Brace
    new Handles
    [Frame_Brace.stl, handle.stl]
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2021-10-25 Add STLs to Z assemblies + adding z motor mount
    [Z Lead screw lower bracket.stl, Z Lead screw upper bracket.stl, Z Lower rod mount clamp.stl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]
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2021-10-25 Update cf tube end.stl
    [cf tube end.stl]
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2022-01-10 fixed enclosure handle
    [handle enclosure.stl, handle.stl]
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2022-01-13 Update foot.stl
    updated foot to include interface layer for printing with no support on bolt holes
    [foot.stl]
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2022-01-26 VzBot EVA Trihorn Printhead update. (#16)
    * Create back_large_duct.stl
    modified VzBot printhead "back" panel to accept the newer (2.4+) layer cooling ducts
    * EVA Trihorn update
    Added a revised back_corexy plate along with matching MGN bottom, to accept the newest EVA Trihorn ducts. These parts must be used together for compatibility. Works with the current VzBot printable p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
    [Trihorn duct High Narrow.stl, Trihorn duct UHF.stl, Trihorn duct default.stl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]
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2022-01-31 Vz-Hextrudort high motor back plate issue fixed
    the rear nut was interfering with the motor. 1mm recess more was add to clear the motor
    [Back plate High motor mount.stl]
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2022-02-10 Adding manual. And updated printer full cad to add V2 of BTT piTFT5 screen
    [Back plate with no tensioner EVA 2.3.stl, Back plate without tensioner EVA 2.4.stl, Belt_clip.stl]
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2022-02-12 Added a hole in the exhaust fan housing for wires
    [Exhaust fan housing.stl]
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2022-02-15 Create Universal face plate-Volcomosq (NF crazy block used with slice heatsink) edition.stl
    [Universal face plate-Volcomosq (NF crazy block used with slice heatsink) edition.stl]
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2022-04-12 Fixed Wiring diagram for cooling fan, and add wiring with CPAP
    [VZBOT 330 WIRING DIAGRAM WITH CPAP.csv, VZBOT 330 WIRING DIAGRAM WITH PART COOLING FAN.csv]
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2022-04-19 Added frame brace right side
    Just a minor update to have the frame braces with correct Vz Logo facing the front. before, one would just print the same one for each side. now with this updated version, one brace STL per side
    [Frame_Brace_left.stl, Frame_Brace_right.stl]
2022-04-19 Create lead screw + lm10luu bracket one piece.stl
    [lead screw + lm10luu bracket one piece.stl]
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2022-04-24 minor fix to BTT pitft5 for V2
    [Frame_Brace.stl, Frame_Brace_right.stl, Rear Screen Cover PiTFT5 version 2.stl]
2022-04-25 Update Universal face plate.stl
    added support for 2.4 eva
    [Universal face plate.stl]
2022-04-25 fixed wiring diagram for Bed sensor connection
    [Universal face plate.stl]
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2022-04-25 Added EVA dragon no v6 grove mount CAD
    [cable holder.stl]
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2022-04-28 updated Eva dragon front clamp for M2.5 8mm bolts
    [Front face dragon no grove mount.stl]
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2022-05-02 LM10LUU bracket tighter to 19.2mm
    [lead screw + lm10luu bracket one piece.stl]
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2022-05-03 Minor: Adding more clearance for t-nuts on all Z parts
    Rod mounts, lead screw mounts, Z motor mounts
    [Z Lead screw lower bracket.stl, Z Lead screw upper bracket.stl, Z Lower rod mount clamp-10mm.stl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]
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2022-05-10 Minor change to the back plate for Vz Logo
    Also added small slot to the motor screws holes for adjustment to the main gear
    [Back plate Low motor mount.stl]
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2022-05-15 added 9mm belt clip + Vcore X stop switch mount
    added 9mm belt clip + Vcore X stop switch mount For aluminum Vz Printhead
    [Belt_clip.stl, X-endstop-mount.stl]
2022-05-15 Vz Hextrudort High motor mount update
    Added the lower right bolt to stiffen the whole assembly like the low motor version
    [Back plate High motor mount.stl]
2022-05-18 added 0.5mm at the bottom of Xstop stopper
    strong part. Minor update
    [XendStop.stl]
2022-06-02 Added CAD for panels
    Also added missing hole on the front right panel for the hinge
    [Panels.step, Vz330_enclsoure_trim .step]
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2022-06-23 Update Panels.step
    Added power switch (C14) holes to rear panels on the left side, so people can mount power switch on either side now
    [Panels.step]
2022-06-27 Corrected Vz-hextrudort high motor version front cover
    The top screw of the front cover was hitting the motor. Now is fine
    [front cover high motor.stl]
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2022-06-30 fixing typo
    [fan duct lower body-trihorn Z scalable spacers.stl]
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2022-07-01 fixe M3 holes in the trihorn duct with brace
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2022-07-01 Corrected holes for nuts on the AWD front idler/motor mounts
    [PulleyMountleftbottom.stl, PulleyMountrightbottom.stl]
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2022-07-17 Fixing top cover rear panel holes position
    The holes on the rear right side (when facing printer) were 0.7mm off
    [Panels.step]
2022-07-23 fixed top cover top panel holes for rear trims
    holes were not aligned properly
    [Panels.step, Vz330_enclsoure_trim .step]
2022-07-29 fixed bot left and right panels of the top cover.
    2 holes were not aligned
    [CPAP fan mount.step, CPAP fan outlet adapter.step, Panels.step]
2022-08-02 update to LSD fan duct. Added lower brace
    [fan duct lower body-brace Z scalable spacers.stl]
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2022-08-31 fixed printed Y gantry bottom part. (minor)
    The bottom right hole for the MGN12 block had a missing fillet/radius
    [Y_gantry_bottom.stl]
2022-09-01 Adding a slicer theme for Prusa and SuperSlicer. (#41)
    * Create read.me
    * Create read.me
    * Create read.me
    * Add files via upload
    * Add files via upload
    * Add files via upload
    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
    [vz330_bed.stl]
2022-09-02 Fixed front door pannels holes for hinges.
    Holes were 3.3mm, now are 4.3mm for M4 bolts
    [Vz330_enclsoure_trim .step]
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2022-09-19 Update Rear panel for CPAP.step
    fix rear pannel position on the CPAP and exhaust fan housing. They were too close to each other
    [Rear panel for CPAP.step]
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2022-10-09 added front LED for AWD mod
    The stock LEDs mounts were colliding with the AWD front motor mounts. Adding new type of LED and mount to clear that.
    [Led mount.step, Led mount.stl]
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2022-10-11 Added CAD for Y gantry back spacers
    MGN12 and MGN9C support
    [Y back spacer MGN12.step, Y gantry MGN9C adapter v1.step]
2022-10-11 Added printed spacers for AWD front motor alu version
    [20mmSpacer.stl, PulleyMountleftbottom.stl, PulleyMountlefttop.stl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]
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2022-11-14 CU5 roll out + new back electronic bay
    [C14 mount.stl, CPAP controller board mounting plate.stl, FlySuper8 din mountX2.stl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]
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2022-11-22 fixing small issue with screen enclosure
    [Screen enclosure.step, screen cover.stl]
2022-12-12 Bed lead screw support update
    minor fix for a hole that was 3.5mm instead of 3mm. It should not have any impact the part but fixing it was needed.
    [LeadScrewSupport.stl]
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2022-12-27 Adding a chain mount option with no drilling for Beta Kits
    [Z-chain mount option2-spacer.stl, Z-chain mount option2.stl]
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2022-12-31 spelling correction.
    [Z stop switch mount AWD version.stl]
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2023-01-02 minor update to fix a fillet radius on the printed Y gantry part
2023-01-04 adding holes in the back panel for Vez's electronic back pack
    [Rear panel for CPAP.dxf, Rear panel for CPAP.step]
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2023-01-05 correcting typo in STL name
    [Vz330 logo plate.stl]
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2023-01-10 Update NEW-VzBoT Official v1.1-CU5.zip
    Fixing back pannel holes for the Electronic Vez Back pack to mount the lower grills
2023-01-11 Bottom and back panel minor update
    -Rear panel: the top 2 holes for wires were too close to the 2040 frame making the use of grommet difficult. Moved inward by 4mm to clear
    -Bottom panel: Added 2 front holes so people can pass wires for the AWD motor from under the printer
    [Panels.step, Rear panel for CPAP.step]
2023-01-11 updating rear panel dxf
    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
    [Rear panel without CPAP.dxf]
2023-01-11 Update NEW-VzBoT Official v1.1-CU5.zip
    Bottom and back panel minor update
    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
2023-01-19 Add files via upload
    bracket for c14 AC power inlet
    [C14 mount.stl]
2023-01-26 Update VZ330 Manual.pdf
    wrong size bolt for the rear top cover hinges in the manual
2023-01-27 Update VZBOT 330 WIRING DIAGRAM AWD WITH CPAP.png
    there was a wire error for the bed thermistor.
2023-01-30 minor fix to front door stopper
    [Front door lower stopper.stl, VzCube.stl]
2023-01-30 fixing a minor mistake on the front cutout for the door stopper
    [Panels.step]
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2023-02-02 Adding Vz-Printhead as default + update to side panels to include RSCS holes
    + Adding VzBoT logo to rear panel DXF
    [Panels.step, Rear panel for CPAP.dxf, Rear panel without CPAP.dxf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]
2023-02-03 Update to RSCS and panels
    -New middle duct for RSCS that is height adjustable now. Require one extra hole in the side panels
    -Updated side panels for RSCS holes. And fixed minor inconsistencies on panels dimensions
    [Lower.stl, Lowerduct.stl, Middle Lower.stl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]
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2023-02-13 Rear panels update
    Added holes for PSU mounting in both back aluminum panel and back electronic acrylic panel. (DXF updated too)
    [Back electronic panel.dxf, Back panel.dxf, Panels.step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]
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2023-03-23 Updating 2WD printed front Idler mounts
    switch from bolts to precision shoulder bolts for Idlers
    [Front Idlers Mount Left BOTTOM.stl, Front Idlers Mount Left TOP.stl, Front Idlers Mount right BOTTOM.stl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]
2023-03-23 Update to single Z printed motor mount
    Adding more adjustment lenght for motor/belt
    [Z motor Lower bracket.stl, Z motor upper bracket.stl]
2023-03-24 V1.2 update
    1- Updated printed single Z motor mount to have more adjustability for z belt and more strength
    2- Updated printed Y gantry (AKA xy joiner) to fix a small miss alignment between smooth idler and rear motors. Minor fix
    3-Updated printed 2WD front idler mounts to use shoulder bolts instead of M5 bolts, and fixed minor misalignment >0.1mm
    4-Updated printed AWD front idlers mounts to have the edge of the parts flush with the frame for easier installation/alignment. + fixing a >0.1mm alignment on idlers position
    5-Updated to Vz-Printhead printed edition with latest revision.
    6-Updated custom bed assembly to use silicon spacer for bed plate instead of springs
    7-fixed hardware error on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
    [PulleyMountleftbottom.stl, PulleyMountlefttop.stl, PulleyMountrightTop.stl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]
2023-03-26 Fixing 2WD front left bottom idler mount support interface layer thickness
    [Front Idlers Mount Left BOTTOM.stl]
2023-03-27 Small update update to lead screw mount for better tolerances
    hole for the bearing went from 22mm to 22.2mm
    [Front Idlers Mount Left TOP.stl, Front Idlers Mount right TOP.stl, Z Lead screw lower bracket.stl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]
2023-03-27 small update on the Z lead screw bearing mount for better tolerances
    hole for bearing went from 22mm to 22.2mm
2023-03-28 Minor: rear left motor tensioner knob cap update
    cap was 9mm long instead of 7mm.
    [knob-cap.stl]
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2023-03-28 Udpate to firmware file
    moved XY motors to port 3-6 instead of 4-7
    [330AWD-printer.cfg, Vez330AWD-printer.cfg, printer-no-cpap.cfg]
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2023-04-26 Small fix on the RSCS holes for M5
    Made the holes a little bigger and slotted for easier installation on the 120mm fan.
    [Lower.stl, Middle upper.stl, spacer_alu_Y_gantry_0.5mm.stl]
2023-05-02 Fix a missing hole on the right side panel
    Hole missing at the bottom front side of the side right panel
    [Panels.step, side panel-Right.dxf]
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2023-06-12 Firmware file update
    -Changed CPAP pin to use PF8 on the Super8 printer.cfg
    -Updated the firmware bin files to have PIN PF8 disabled when klipper doesn't run.
    [330AWD-printer.cfg]
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2023-07-17 update to Mellow Fly 5" screen enclosure (front only)
    [Front cover.stl]
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2023-09-03 Various QOL Changes (#60)
    * Moved EVA printhead to Deprecated Folder
    Moved CAD + Stls to the EVA Section.
    * Various QOL Changes
    Moved the macros to be with the main klipper files since they are required.
    Better Explained The Vz-Printhead sections/ Linked to them with CAD + STLs.
    * QOL Changes
    Added Section to link to the docs.
    * Added Klipper Linux Setup
    Explained adding the Linux Process from klipper.
    * Formatting
    * Update README.md
    * Update README.md
    Fixed BOM link mistake
    [Back plate with no tensioner EVA 2.3.stl, Back plate with tensioner EVA 2.3-6028fan.stl, Back plate with tensioner EVA 2.3.stl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]
2023-09-15 Updated foot spacer for Mellow KIT
    now is 3.6mm to fit the rubber feet from mellow kit
    [Spacer.stl]
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2023-10-05 fixed wiring diagram.
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2023-11-28 Create pulley spacer short bottom.stl
    [pulley spacer short bottom.stl]
2023-12-11 Spacer fixed. Hole was missing
    [Spacer.stl]
2024-01-31 Fixed size for new alu X beam
    made hole spacing 21.2mm instead of 20.2mm
    [Y_gantry_bottom_left.stl, Y_gantry_bottom_right.stl, Y_gantry_top_left.stl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]
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2025-01-02 Readme: Small CSS tweak, small text tweak (#68)
    Tweaked some letters/words in text for reading flow. Added proper markup to the Ko-Fi image that falls back to vertical-align if float isn't allowed/available. Should prevent it from completely outsizing the header it's positioned in.
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2025-03-10 Update README.md
    fixed CAD online model URL
